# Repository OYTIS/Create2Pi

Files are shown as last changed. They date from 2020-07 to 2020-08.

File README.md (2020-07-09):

# Pi HAT for iRobot Create

iRobot Create Open Interface is a 7-pin mini-DIN connector exposing unregulated battery power pin and 5V UART. The HAT contains a power regulator to convert the battery power to 5V, and a level shifter to interface Roomba UART with Raspberry's 3.3V UART. Also a USB-Serial interface is added for convenience.

## Quickstart
TODO (when software is done)

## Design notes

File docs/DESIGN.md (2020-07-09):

### Power
According to iRobot [documentation](https://www.irobotweb.com/~/media/MainSite/PDFs/About/STEM/Create/iRobot_Roomba_600_Open_Interface_Spec.pdf), it has a resettable fuse that would cut the power supply if regular current draw gets above 200mA or if there is a peak above 500mA. Typical voltage of iRobot battery is 14.4V, while it stops working when this voltage drops below 12.5V, which is the minimum voltage we want to support. That means that we want to draw no more than 2.5W with maximum allowed peaks of 6.25W.

According to [Raspberry Pi FAQ](https://www.raspberrypi.org/documentation/faqs/#pi-power) Raspberry Pi Zero W would draw about 230mA or 1.15W at 5V when actively performing tasks like video playback. Raspberry Pi 3B will draw 550mA or 2.75W, and the peak draw is 850mA or 4.25W.

It means that in ideal case where no power is lost in the conversion, Pi Zero W should work without a problem, while Pi 3B has some chance to work when the battery is fully charged.

It also means that we want the power conversion to be as efficient as possible which dictates that a buck converter is used. To simplify design, a buck module is used, namely [LMZ21701](https://www.ti.com/lit/ds/symlink/lmz21701.pdf). In the area that is interesting to us, its efficiency is about 90%, which makes the draw from the battery 1.28W for Pi Zero and 3.06W for Pi 3B. The latter rules out Pi 3B even for the fully charged battery, so we'll focus on Pi Zero. That dictates...

### Form factor
Primary platform is Raspberry Pi Zero (W), so the form factor is that of Pi Zero.

### Connector
Ideally we would want a 7-pin mini-DIN connector on the board, but turns out these are rare, available with large MOQs and long lead times. This is a hobby project, and a project for hobbyists, so we can't afford this. For simplicity a 5-pin screw connector is used. It is recommended to use it together with Adafruit's [cable](https://www.adafruit.com/product/2438), or you can make your own of course. One extra NC pin (apart from the connected VCC. GND, RX and TX) is added to help manage dangling DD/BRC wire from the cable.

Alternatively you could modify the design to make 7 holes in the shape of a male mini-DIN plug instead of the screw connector, and solder long enough pins there. It should work, but will make the design less physically flexible.

### Other
All parts are located on one side for the ease of manufacturing. The buck module is unfortunately not hand-solderable though.

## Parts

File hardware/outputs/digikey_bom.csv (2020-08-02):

Manufacturer Part Number | Manufacturer | Digi-Key Part Number | Quantity | Unit Price | Extended Price | Description
CC0402JRX7R9BB332 | Yageo | 311-3769-1-ND | 1 | 0.09 | 0.09 € | CAP CER 3300PF 50V X7R 0402
GRM21BR61E226ME44K | Murata Electronics | 490-14661-1-ND | 2 | 0.49 | 0.98 € | CAP CER 22UF 25V X5R 0805
CC0402ZRY5V7BB104 | Yageo | 311-1047-1-ND | 3 | 0.09 | 0.27 € | CAP CER 0.1UF 16V Y5V 0402
XZMDK68W-2 | SunLED | 1497-1174-1-ND | 1 | 0.39 | 0.39 € | LED RED CLEAR CHIP SMD
XZVG68W-2 | SunLED | 1497-1219-1-ND | 1 | 0.45 | 0.45 € | LED GREEN CLEAR CHIP SMD
LMZ21701SILT | Texas Instruments | 296-38545-1-ND | 1 | 4.26 | 4.26 € | DC DC CONVERTER 0.9-6V 6W
1050170001 | Molex | WM1399CT-ND | 1 | 0.83 | 0.83 € | CONN RCPT USB2.0 MICRO B SMD R/A
TXS0102DCTR | Texas Instruments | 296-21978-1-ND | 1 | 0.51 | 0.51 € | IC TRNSLTR BIDIRECTIONAL SM8
NUP2202W1T2G | ON Semiconductor | NUP2202W1T2GOSCT-ND | 1 | 0.52 | 0.52 € | TVS DIODE 5V 20V SC88
FT230XS-R | FTDI, Future Technology Devices International Ltd | 768-1135-1-ND | 1 | 1.85 | 1.85 € | IC USB SERIAL BASIC UART 16SSOP
RC0402JR-0756RL | Yageo | 311-56JRCT-ND | 2 | 0.09 | 0.18 € | RES SMD 56 OHM 5% 1/16W 0402
RT0402FRE0710KL | Yageo | YAG1233CT-ND | 1 | 0.09 | 0.09 € | RES SMD 10K OHM 1% 1/16W 0402
RC0402FR-07232KL | Yageo | YAG3062CT-ND | 1 | 0.09 | 0,09 € | RES SMD 232K OHM 1% 1/16W 0402
RC0402FR-0744K2L | Yageo | YAG3163CT-ND | 1 | 0.09 | 0.09 € | RES SMD 44.2K OHM 1% 1/16W 0402
BAT54C-7-F | Diodes Incorporated | BAT54C-FDICT-ND | 1 | 0.17 | 0.17 € | DIODE ARRAY SCHOTTKY 30V SOT23-3
MD-80SM | CUI Devices | CP-2280-ND | 1 | 1.87 | 1.87 € | CONN RCPT FMALE MINI DIN 8P SLDR
GRM155R60J475ME47D | Murata Electronics | 490-5915-1-ND | 1 | 0.099 | 0.99 € | CAP CER 4.7UF 6.3V X5R 0402
PPTC202LFBN-RC | Sullins Connector Solutions | S6104-ND | 1 | 2.03 | 2.03 € | CONN HDR 40POS 0.1 TIN PCB

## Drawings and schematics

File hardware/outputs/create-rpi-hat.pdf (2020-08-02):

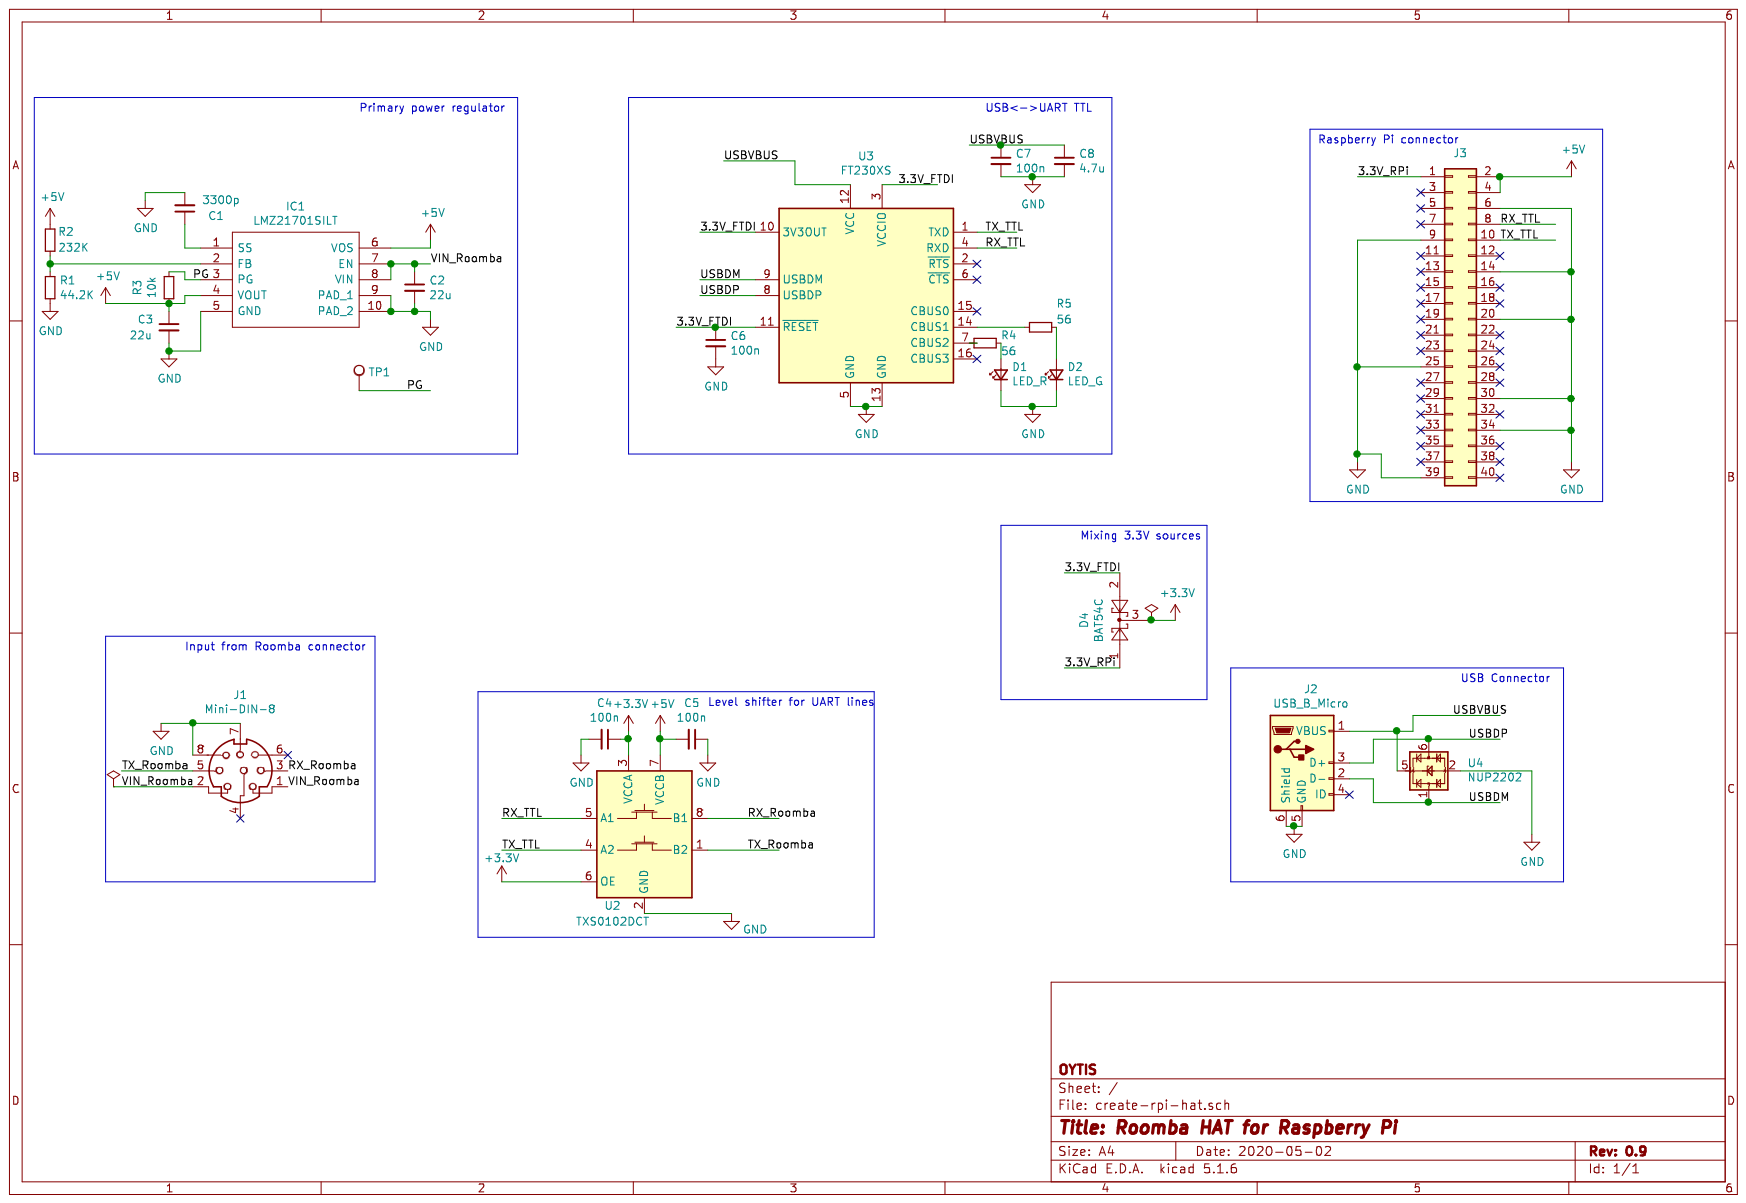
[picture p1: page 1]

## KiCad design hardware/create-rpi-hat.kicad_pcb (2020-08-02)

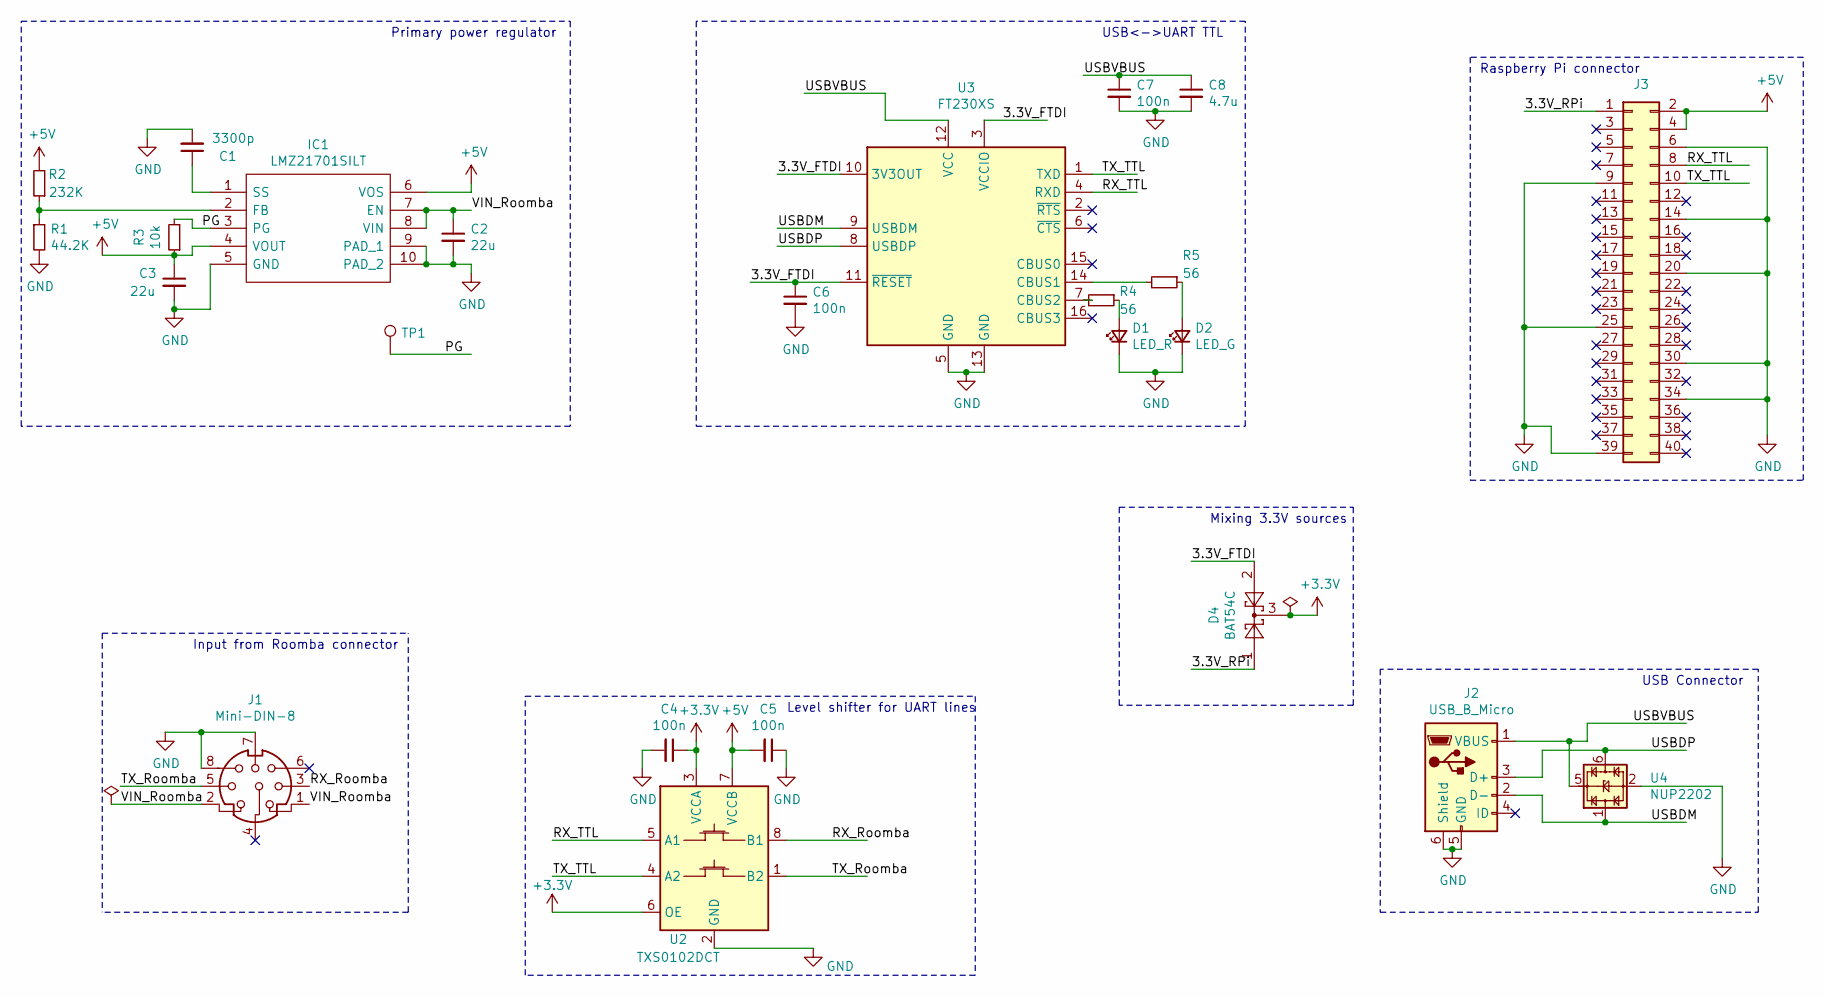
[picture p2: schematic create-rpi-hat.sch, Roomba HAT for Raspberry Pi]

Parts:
C1: 3300p; C_0402_1005Metric
C2, C3: 22u; C_0805_2012Metric_Pad1.15x1.40mm_HandSolder
C4, C5, C6, C7: 100n; C_0402_1005Metric
C8: 4.7u; C_0402_1005Metric
D1: LED_R; R_0402_1005Metric
D2: LED_G; R_0402_1005Metric
D4: BAT54C; SOT-23
IC1: LMZ21701SILT; SIL0008E; Mouser Part Number 595-LMZ21701SILT
J1: Mini-DIN-8; CUI_MD-80SM
J2: USB_B_Micro; USB_Micro-B_Molex-105017-0001
J3: RaspberryPi GPIO connector; PinSocket_2x20_P2.54mm_Vertical
R1: 44.2K; R_0402_1005Metric
R2: 232K; R_0402_1005Metric
R3: 10k; R_0402_1005Metric
R4, R5: 56; R_0402_1005Metric
TP1: TestPoint; TestPoint_Pad_D2.0mm
U2: TXS0102DCT; SSOP-8_2.95x2.8mm_P0.65mm
U3: FT230XS; SSOP-16_3.9x4.9mm_P0.635mm
U4: NUP2202; SOT-363_SC-70-6

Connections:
+3V3: C4.1, D4.3, U2.3 (VCCA), U2.6 (OE)
+5V: C3.1, C5.2, IC1.4 (VOUT), IC1.6 (VOS), J3.2, J3.4, R2.2, R3.1, U2.7 (VCCB)
/3.3V_FTDI: C6.1, D4.2, U3.3 (VCCIO), U3.10 (3V3OUT), U3.11 (~RESET)
/3.3V_RPi: D4.1, J3.1
/PG: IC1.3 (PG), R3.2, TP1.1
/RX_Roomba: J1.3, U2.8 (B1)
/RX_TTL: J3.8, U2.5 (A1), U3.4 (RXD)
/TX_Roomba: J1.5, U2.1 (B2)
/TX_TTL: J3.10, U2.4 (A2), U3.1 (TXD)
/USBDM: J2.2 (D-), U3.9 (USBDM), U4.1
/USBDP: J2.3 (D+), U3.8 (USBDP), U4.6
/USBVBUS: C7.1, C8.1, J2.1 (VBUS), U3.12 (VCC), U4.5
/VIN_Roomba: C2.1, IC1.7 (EN), IC1.8 (VIN), J1.1, J1.2
GND: C1.2, C2.2, C3.2, C4.2, C5.1, C6.2, C7.2, C8.2, D1.1 (K), D2.1 (K), IC1.5 (GND), IC1.9 (PAD_1), IC1.10 (PAD_2), J1.7, J1.8, J2.5 (GND), J2.6 (Shield), J3.6, J3.9, J3.14, J3.20, J3.25, J3.30, J3.34, J3.39, R1.2, U2.2 (GND), U3.5 (GND), U3.13 (GND), U4.2
unnamed: C1.1, IC1.1 (SS)
unnamed: D1.2 (A), R4.1
unnamed: D2.2 (A), R5.1
unnamed: IC1.2 (FB), R1.1, R2.1
unnamed: R4.2, U3.7 (CBUS2)
unnamed: R5.2, U3.14 (CBUS1)

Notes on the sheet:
Input from Roomba connector
Primary power regulator
Level shifter for UART lines
USB<->UART TTL
USB Connector
Raspberry Pi connector
Mixing 3.3V sources

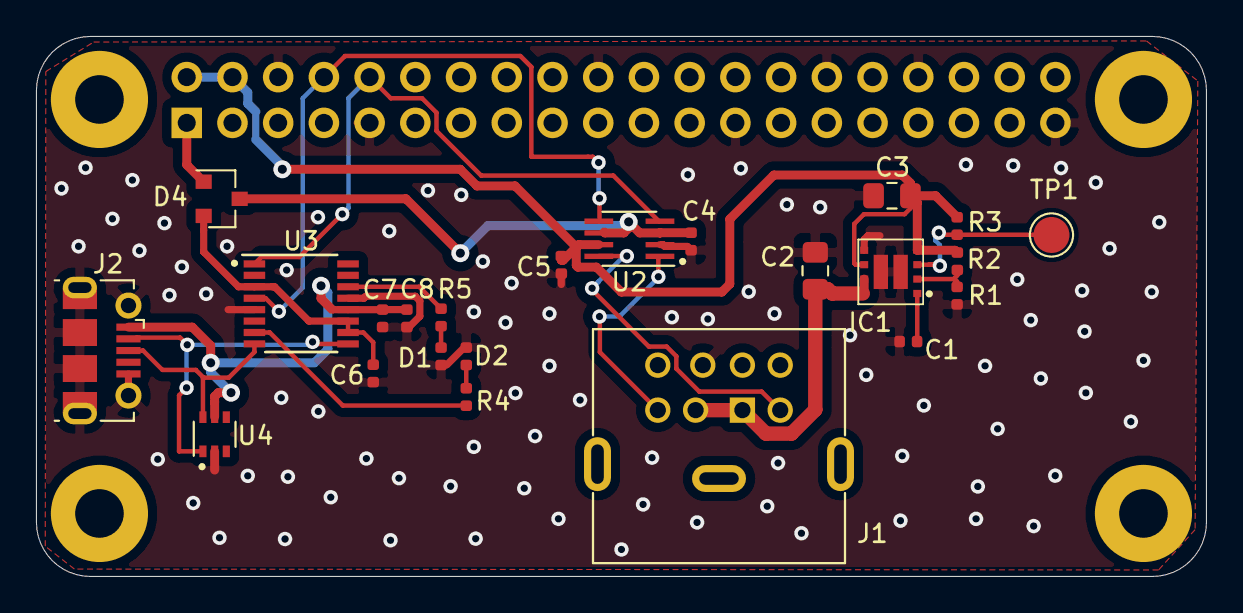
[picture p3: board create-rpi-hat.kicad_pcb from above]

Board: 2 copper layers, 65.0 x 30.0 mm, 24 parts (1 on the bottom side), 20 nets.

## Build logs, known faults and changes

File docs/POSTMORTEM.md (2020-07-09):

# Rev 0.8 (Aisler)
## What was good?
  * 5V works
## What was bad?
  * WRONG CONNECTION ON TXS0102: `3.3V` should be the `A` side, `5.0V` should be the `B` side
  * WRONG CONNECTION ON FT230: `RX` should go to `RX_TTL`, `TX` should go to `TX_TTL`
  * Missing decoupling capacitor on USB VBUS
  * Missing bypass capacitor on FT230X
  * Missing silkscreen PIN 1 designators on ICs
  * Gaps in component numbering (D1, D2, D4)
  * Numbering doesn't correspond to placement
  * Roomba connector (J1) is too massive.
  * No Roomba power LED.
  * No Power Good LED.
  * No screw holes in the corners
## What can be improved?
  * Mini DIN 8 socket instead of screw connector

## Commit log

2020-05-14 Initial commit (hopefully with a working hardware design)
    [create-rpi-hat.kicad_pcb, create-rpi-hat.sch]
2020-05-17 Removed power pours and made more space for the buck module
    The latter is against module's layout recommendations, but makes
    soldering/rework easier
    [create-rpi-hat.kicad_pcb, create-rpi-hat.sch]
2020-06-01 Add a bit of vanity
    [create-rpi-hat.kicad_pcb]
2020-06-01 Add Digikey BOM
    [digikey_bom.csv]
2020-07-09 First revision (ordered on Aisler) and postmortem
    [create-rpi-hat.kicad_pcb]
2020-08-02 Revision 0.9 (also ordered on Aisler)
    [create-rpi-hat.kicad_pcb, create-rpi-hat.sch, digikey_bom.csv]
